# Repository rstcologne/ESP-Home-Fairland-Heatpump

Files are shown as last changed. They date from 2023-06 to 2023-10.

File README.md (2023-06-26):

# ESP-Home-Fairland-Heatpump

I'd like to share my approach to control a Fairland made heatpump directly via modbus not depending on Tuya with homeassistant. My heatpump is an IPS Pro model sold by Pool Systems which seems to be quite similar to the InverX series by Fairland directly. 

## Disclaimer

Everything I describe here is at quality level "works for me". Follow these instructions at your own risk. You need to open your heatpump and connect cables to the mains powered main crontrol board. It might void your warranty and you will get close to mains powered components including some large capacitors. Don't follow allong if you are not sure what you are doing. 

## Preparing the ESP Home board
### Components used:
- ESP Baord. Most will work
- MAX485 module, preferably one with automatic flow control
- Buck converter if the 12V from the heatpump control board will be used to power the ESP
- JST-XH 4 pin connector to attach everything to the control board
- other connectors (optional) to alow for easier disassembly

### Wiring
- 12V+ from control board to + on the buck converter input side
- Ground from control board to - on the buck converter input side
- out + from buck converter to 5V or VIN of the ESP board
- out - from buck converter to GND on the ESP board
- RX on ESP to RXD on max485 board
- TX on ESP to TXD on max485 board
- 3,3v on ESP to VCC on max485  board
- G on ESP to GND on max485 board
- A on max485 board to A on control board
- B on max485 board to B on control board

If you use a variable voltage buck converter, make sure to set it properly to deliver 5v from 12v input before connecting it to the ESP. Otherwise you might fry the board. 

In case you are using a max485 board without automatic flow control, one additional pin needs to be connected to the two center pins on the max board. This needs to be configured in esphome as well. 

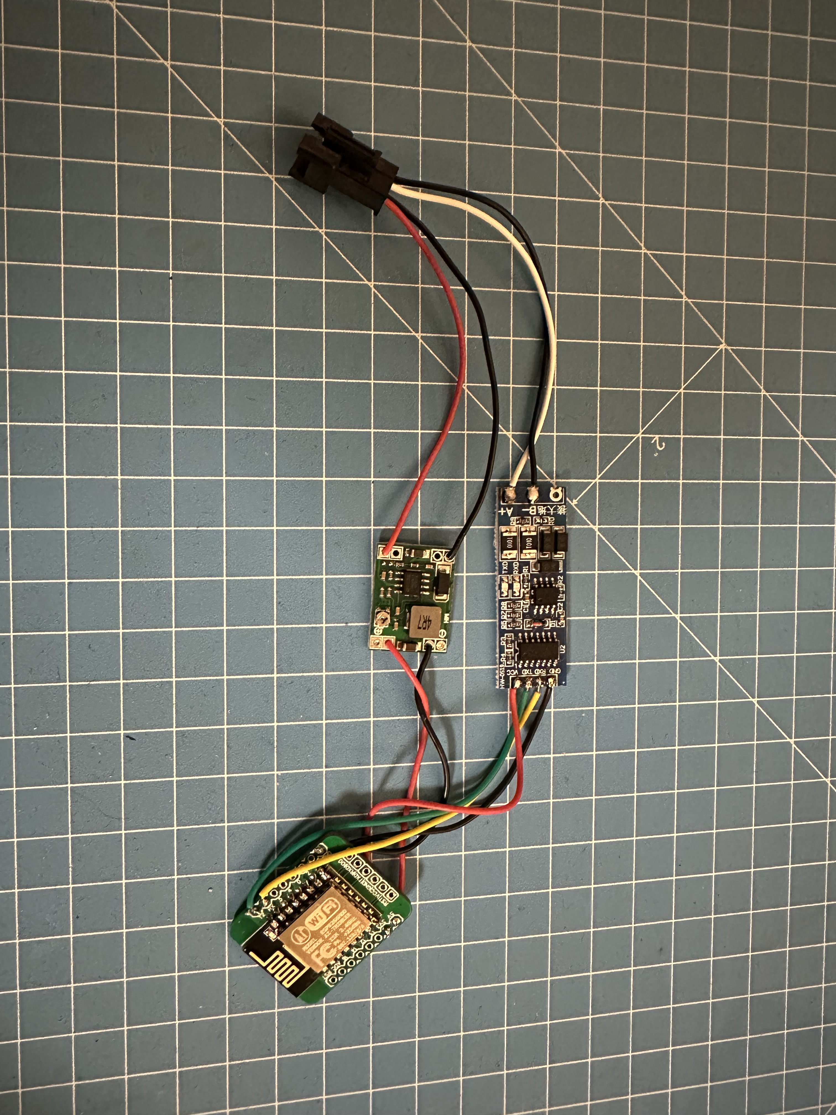
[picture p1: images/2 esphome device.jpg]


## ESP-Home
1. Create a new ESPHome device in homeassistant
2. Copy the esphome config snippet below the header. I left the captive_portal directive in the snippet for reference. Make sure it's only there once.
3. Flash the board

## Connecting to heatpump
Connect everything to the header in the center of the image marked B A G +12V. The existing cable channels are quite handy to feed the cable out at the back of the unit. I have included a very simple (temporary) housing for the electronics which I clip on to one of the 50mm water pipes. 

### How to open the heatpump (for my unit)
- Open the side panel providing access to the power connection terminal with two screws at the bottom
- two additional screws free the panel above which houses the control unit. remove this panel and disconnect the control unit
- Remove the two screws holding the top plate. There's an additional screw at the back to remove. After that, the top can be lifted.
- There's a large padded box in the center of the unit. Open it and inside you'll find the control board

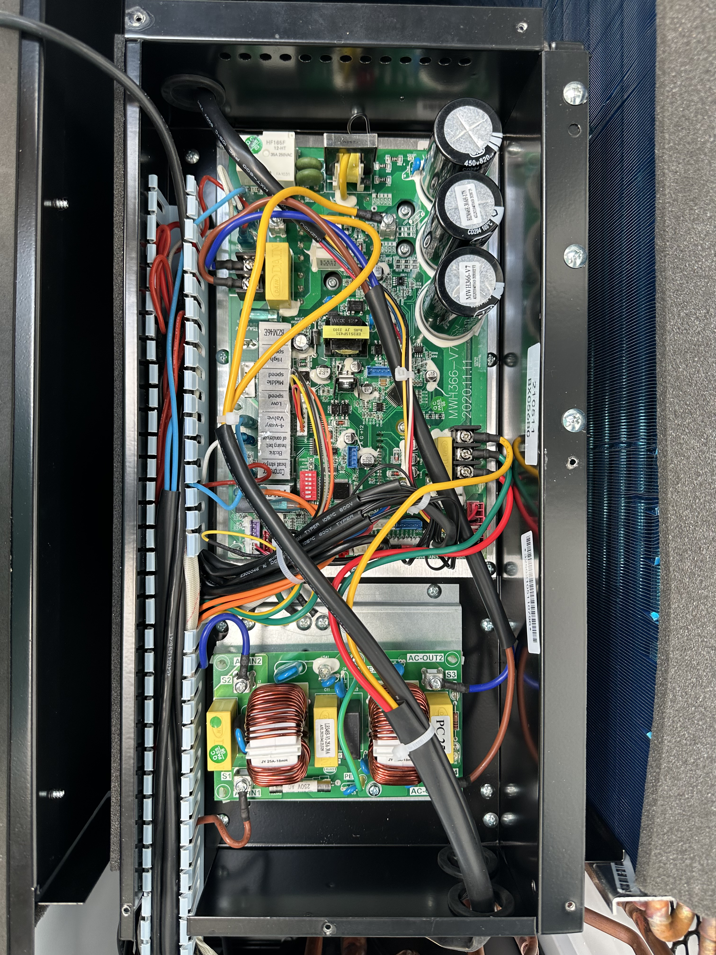
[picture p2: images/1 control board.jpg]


## Dashboard
I have added a code snippet you can incorporate in your dashboard. 
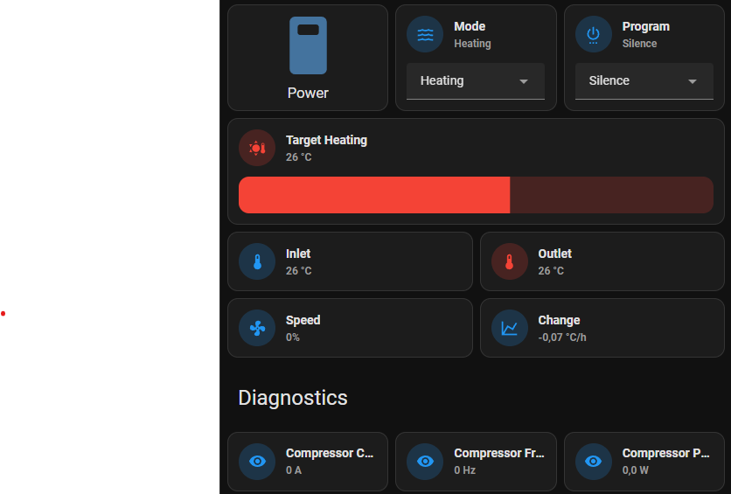
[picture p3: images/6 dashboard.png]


### Known issues
- The modbus configuration still throws a few warnings related to duplicate entries. It seems to work well despite these warnings though.
- The selected heating/cooling mode (slient, normal, ...) is not remembered properly. The heatpumpt often switches to silent when it's powered on even though normal was selected before.
- The case is to be considered rather preliminary. I just wanted something to get it to work.

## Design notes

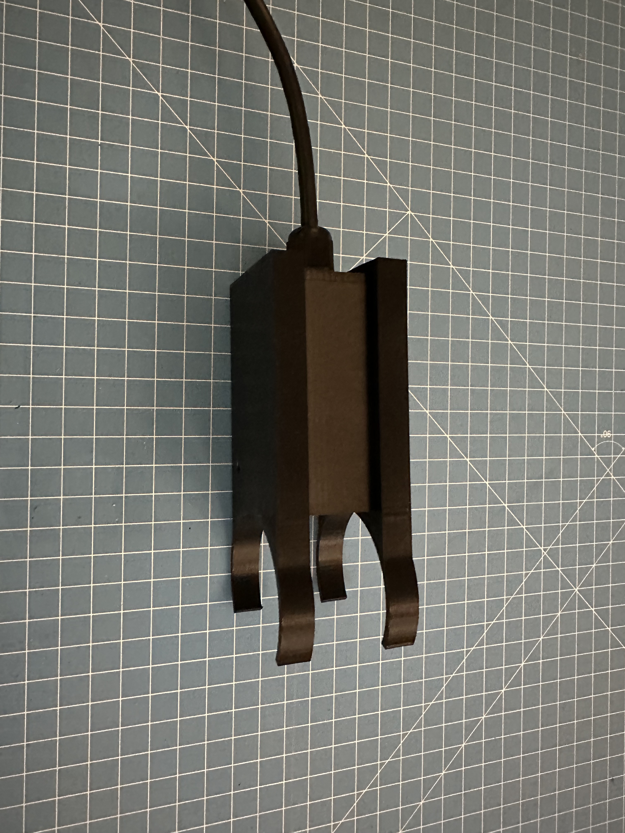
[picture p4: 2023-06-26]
images/4 case 2.jpg

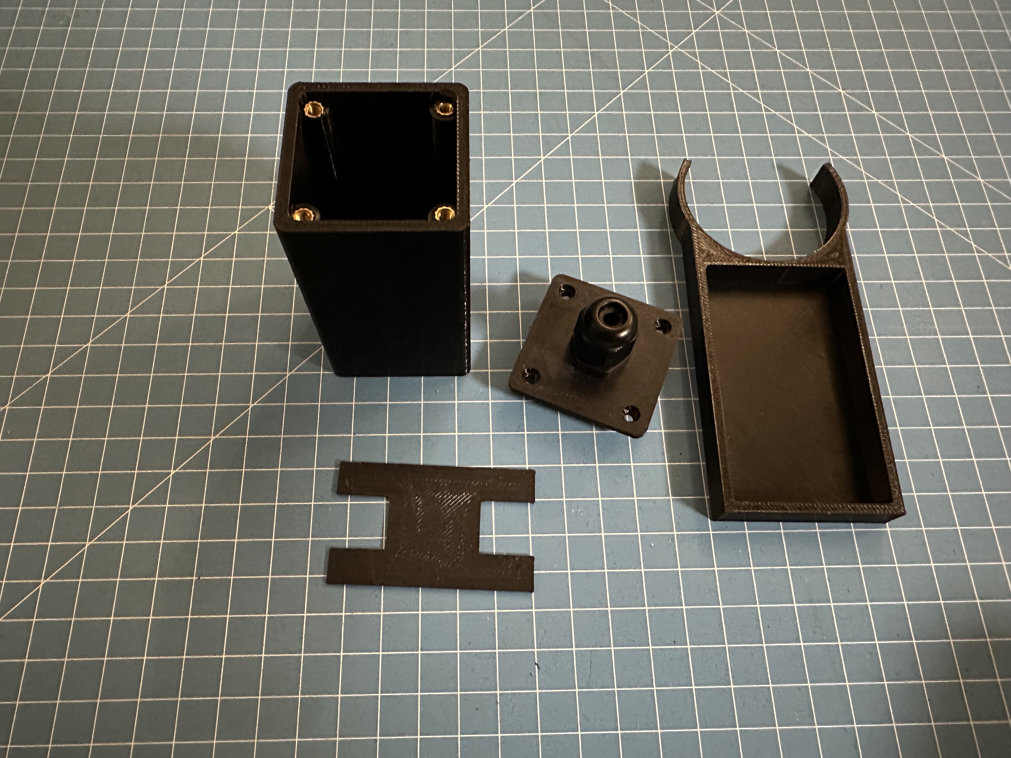
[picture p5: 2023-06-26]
images/3 case 1.jpg

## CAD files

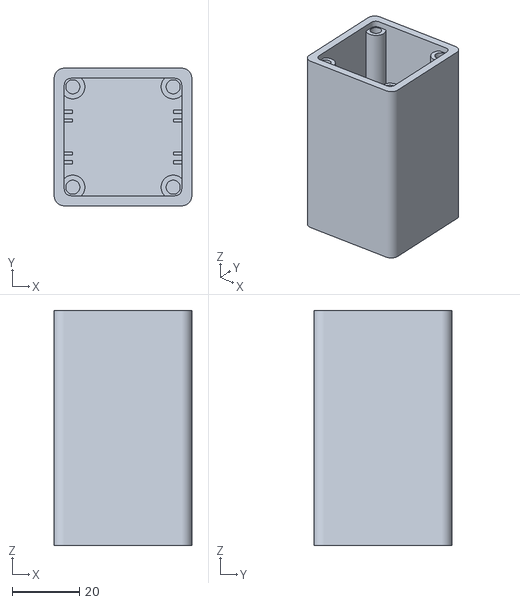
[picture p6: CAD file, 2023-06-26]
case/PoolPump_Electronics-Case.stl
41.0 x 41.0 x 70.0

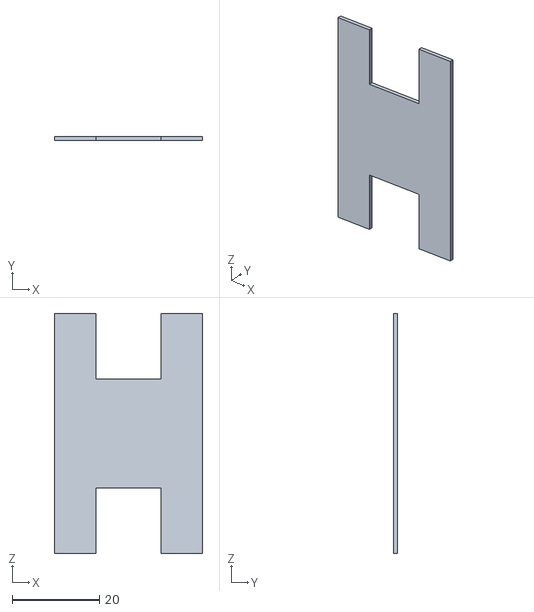
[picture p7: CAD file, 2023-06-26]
case/PoolPump_Electronics-Divider.stl
34.0 x 1.00 x 55.0

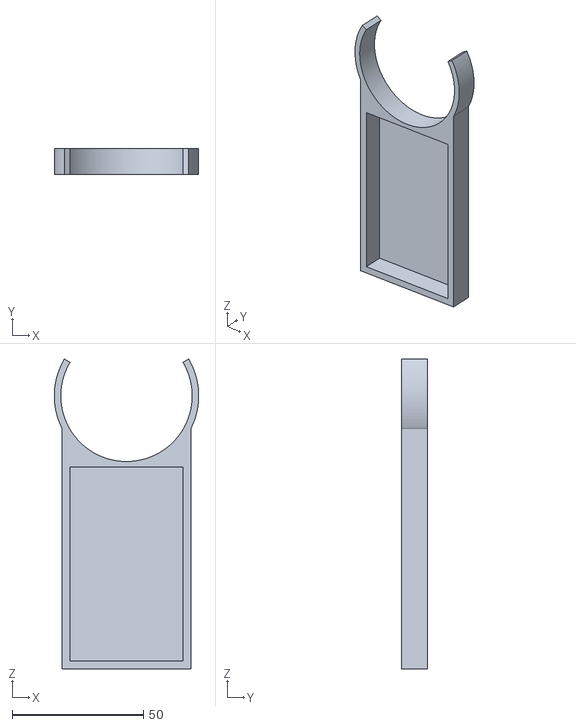
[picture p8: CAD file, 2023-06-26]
case/PoolPump_Electronics-Mount.stl
55.0 x 10.0 x 118.0

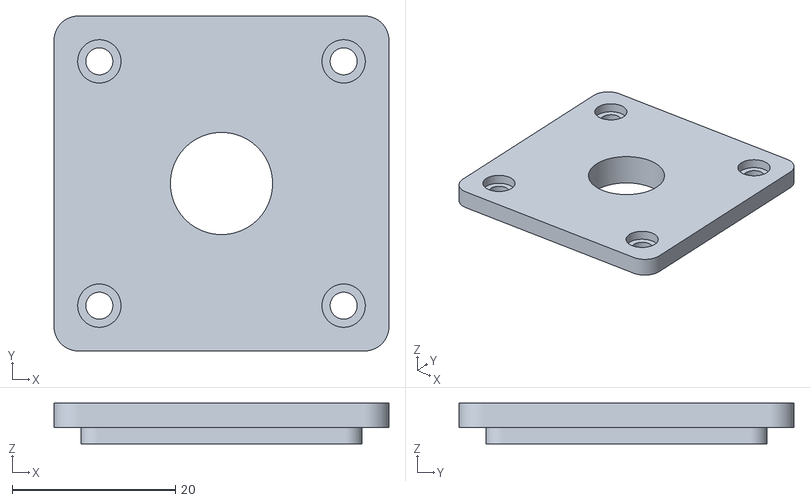
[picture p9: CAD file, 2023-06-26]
case/PoolPump_Electronics-Lid.stl
41.0 x 41.0 x 5.00

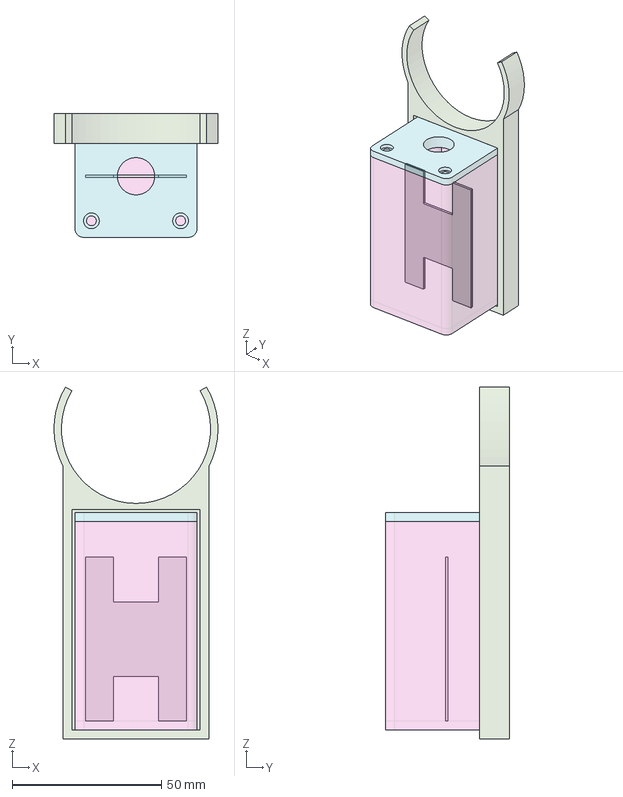
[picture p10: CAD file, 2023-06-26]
case/PoolPump_Electronics.FCStd
55.0 x 41.5 x 118.0 mm
Case
Lid
Mount
Divider

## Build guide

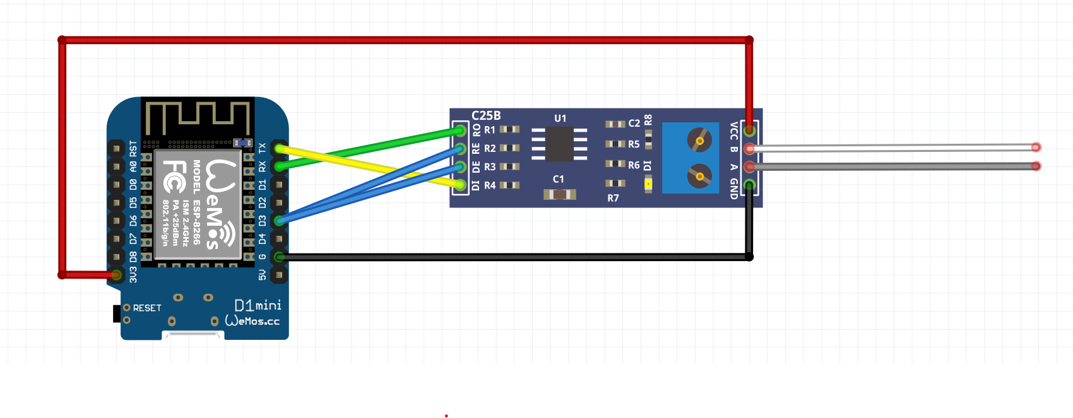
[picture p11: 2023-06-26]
images/5 wiring.png

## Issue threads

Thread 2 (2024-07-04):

Compatibility with other Tuya comatible Heatpumps

chrisguen, 2024-07-04:
Hello, has anyone tested if this project works with other wifi/tuya enabled heatpumps like [this](https://www.poolmegastore.de/poolheizung/waermepumpen/full-inverter-waermepumpen/evolution-proline/full-inverter-waermepumpe-evolution-proline-7.html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) one?

raspitoaster, 2024-07-09:
Hi, I am testing with a "Evolution Baseline" - but without success yet.
There are two RS485 sockets on the  circuit board. The #1 is empty, the #2 has the front panel (display/buttons) and WiFi connected.
Using the YAML here on a NodeMCUv2 (ESP8266/4M) connected to a RS485-2-TTL converter results in many "Duplicate modbus command found" warnings and (only) silly sensor readings.
I tested the setup (NodeMCU/ESPHome/RS485-2-TTL converter) connected to a second RS485-2-TTL converter and a RASPI with pyModSlave simulating a modbus device. This works perfectly, but there are many posts around that claim ESP8266 with software serial will not work at all and ESP32 with hardware serial must be used.

raspitoaster, 2024-07-10:
Update: just tried with an ESP32 and hardware serial ... same result.

poorredneck, 2025-07-23:
Works great on my Raypak (Rheem) Crosswinds 65i.
Board is similar but not the same, same blue JST "BAG +12" connector.

poorredneck, 2025-07-23:
@raspitoaster were you asking OP or me? Mine is no different than the original from rstcologne, all the registers lined up. I dont have a way of checking the error codes, but the E3 for no water flow does work correctly, as well as all the temperatures and set point/mode adjustments. The Raypak does not have a "Turbo" mode. I also didn't know mine had "Super Silent" that option was not available in the app or on the LCD interface but does work via the ModBus commands.

Incase you were asking me and not OP, here is my config.

```
esphome:
  name: poolheater
  friendly_name: Pool Heater

esp8266:
  board: d1_mini

wifi:
  ssid: "Repeater"
  password: !secret wifi_pw
  ap:
    ssid: "PoolHeater Fallback AP"
    password: "fallback123"

logger:
  level: DEBUG

api:
  encryption:
    key: !secret encrypt1

ota:
  - platform: esphome

####
## Create a new ESP-Home Device and paste the snippet below into the newly created config.
## make sure, captive portal is only in the file once (if you want to keep it in the first place)
####

uart:
  id: mod_bus
  rx_pin: D2
  tx_pin: D1
  baud_rate: 9600

modbus:
#  flow_control_pin: GPIO4
  id: modbus1

modbus_controller:
  - id: fairland
    ## the Modbus device addr
    address: 0x0001
    modbus_id: modbus1
    update_interval: 10s

###################################################
# Elements with Modbus Operation read 01 / write 05
# coil
###################################################
# 0	Power
# 1	compulsory defrosting
# 2～47	reserve
###################################################

switch:
  - platform: modbus_controller
    modbus_controller_id: fairland
    name: "PWP Power Switch"
    id: pwp_power_switch
    register_type: coil
    address: 0x0
    # unit_of_measurement: "State"

###################################################
# Elements with Modbus Operation read 03 / write 06
# holding
###################################################
# address content	Range	Unit	Step length	Defaut	Illustration
# 0	mode selectioin 1	0～2				0：Auto，1：Heating，2：Cooling
# 1	mode selectioin 2	0～3		1	1	0：Normal，1：silence，2：Super silence, 3: Turbo
# 2	Temp setting under Auto mode	18~35	℃	1	25
# 3	Temp setting under heating mode
# 4	Temp setting under cooling mode	30~95	%	1	50
# 5	Running mode of water pump	0~2		1	0	"0：Continuation
# 1：Water temp control
# 2：time/water temp control
# "
# 6	Time setting of water pump (When under running mode 2)	10 ~ 120 	min	5	60
# 7	The compressor runs continuously before defrosting enters	20~90	min	1	20
# 8	Defrosting start temp	-10~10	℃	1	-1
# 9	Defrosting running time	1~12	min	1	8
# 10	Defrosting quit temp	0~30	℃	1	8
# 11	Fixed speed mode selection
# 12	reserve
# 13	reserve
# 14	Low temperature shutdown protection correction amount
# 12	reserve
# 13	reserve
# 17	Electronic expansion valve overheat level（heating）	-10~20	℃	1	3
# 18	Electronic expansion valve overheat level（cooling）	-10~20	℃	1	3
# 19	Electronic expansion valve manual/auto	0~1		1	0	0：auto，1：Manual
# 20	Electronic expansion valve openning setting（heating）	50~240		2	100
# 21	Electronic expansion valve openning setting（cooling）	50~240		2	100
# 22	The medium frequency ratio selection
# 23	reserve
# 24	reserve
# 25	Power off memory function	0~1		1	1	0: None;  1: Yes
# 26	reserve
# 27	reserve
# 28	reserve
# 29	reserve
# 30	reserve
# 31	reserve
# 32	reserve
###################################################

select:
  - platform: modbus_controller
    name: "PWP Operating Mode"
    id: pwp_operating_mode
    modbus_controller_id: fairland
    address: 0x0
    value_type: U_WORD
    optionsmap:
      "Auto": 0
      "Heating": 1
      "Cooling": 2

  - platform: modbus_controller
    name: "PWP Power Mode"
    id: pwp_power_mode
    modbus_controller_id: fairland
    address: 0x1
    value_type: U_WORD
    optionsmap:
      "Super Silence": 2
      "Silence": 1
      "Normal": 0
      "Turbo": 3

# Temperature Formula
# ((value - 96) / 2) + 18

number:
  - platform: modbus_controller
    modbus_controller_id: fairland
    name: "PWP Target Temperature Heating"
    id: pwp_target_temperature_heating
    register_type: holding
    address: 0x3
    value_type: U_WORD
    unit_of_measurement: "°F"
    min_value: 64        # 18 °C → 64.4 °F, rounded to 64
    max_value: 104     # 32 °C → 89.6 °F, rounded to 90
    step: 1              # only allow integer °F steps
    lambda: |-
      // read raw R → °F, rounded to nearest integer
      return round((x - 60) * 0.9 + 32);
    write_lambda: |-
      // take integer °F → raw R
      float raw = (x - 32) / 0.9 + 60;
      return (uint16_t)raw;

  - platform: modbus_controller
    modbus_controller_id: fairland
    name: "PWP Target Temperature Auto"
    id: pwp_target_temperature_auto
    register_type: holding
    address: 0x2
    value_type: U_WORD
    unit_of_measurement: "°F"
    min_value: 54        # 18 °C → 64.4 °F → 64 °F
    max_value: 104        # 32 °C → 89.6 °F → 90 °F
    step: 1
    lambda: |-
      // raw R → °F: round((R–60)/2×1.8 + 32)
      return round((x - 60) * 0.9 + 32);
    write_lambda: |-
      // °F → raw R: (F–32)/0.9 + 60
      float raw = (x - 32) / 0.9 + 60;
      return (uint16_t)raw;

  - platform: modbus_controller
    modbus_controller_id: fairland
    name: "PWP Target Temperature Cooling"
    id: pwp_target_temperature_cooling
    register_type: holding
    address: 0x4
    value_type: U_WORD
    unit_of_measurement: "°F"
    min_value: 54        # 18 °C → 64.4 °F → 64 °F
    max_value: 86        # 32 °C → 89.6 °F → 90 °F
    step: 1
    lambda: |-
      // raw R → °F: round((R–60)/2×1.8 + 32)
      return round((x - 60) * 0.9 + 32);
    write_lambda: |-
      // °F → raw R: (F–32)/0.9 + 60
      float raw = (x - 32) / 0.9 + 60;
      return (uint16_t)raw;

###################################################
# Elements with Modbus Operation read 04 / write NA
# read
###################################################
# 0	Percentage of speed
# 1	Target frequency of compressor
# 2	Voltage of PFC
# 3	Inlet water temp
# 4	Outlet water temp
# 5	Ambient air temp
# 6	Dircharge temp
# 7	Outer coil pipe temp
# 8	Suction temp
# 9	Inner coil pipe tem
# 10	Running frequency of compressor
# 11	Current of compressor
# 12	Cooling plate temp
# 13	Electronic expansion valve opening
# 14	DC fan speed
# 15	Lower limit of setting temp of auto mode
# 16	Upper limit of setting temp of auto mode
# 17	Lower limit of setting temp of heating mode
# 18	Upper limit of setting temp of heating mode
# 19	Lower limit of setting temp of cooling mode
# 20	Upper limit of setting temp of cooling mode
# 21	Motherboard version code1					ASCII code
# 22	Motherboard version code2					ASCII code
# 23	Motherboard version code3					ASCII code
# 24	Motherboard version code4					ASCII code
# 25	Motherboard version code5					ASCII code
# 26	Model code1					ASCII code
# 27	Model code2 ('C'is heating and cooling version，‘H’is heating version)					ASCII code
# 28	Model code3					ASCII code
# 29	Model code4					ASCII code
# 30	Voltage of power supply		V	1
# 31	The remaining time of Compressor shutdown protection 		S	1
# 32	reserve
###################################################

sensor:

  - platform: modbus_controller
    modbus_controller_id: fairland
    name: "PWP Speed Percentage"
    id: pwp_speed_percentage
    register_type: read
    address: 0x0
    value_type: U_WORD
    unit_of_measurement: "%"

  - platform: modbus_controller
    modbus_controller_id: fairland
    name: “Voltage of PFC”
    id: voltage_of_pfc
    register_type: read
    address: 0x2
    value_type: U_WORD
    unit_of_measurement: "V"

  - platform: modbus_controller
    modbus_controller_id: fairland
    name: "PWP Inlet Water Temperature"
    id: pwp_inlet_water_temperature
    register_type: read
    address: 0x3
    value_type: U_WORD
    unit_of_measurement: "°F"
    filters:
      - offset: -60      # (raw – 60)
      - multiply: 0.9    # × 0.9 → (raw–60)/2×1.8
      - offset: 32       # + 32 to finish °C→°F

  - platform: modbus_controller
    modbus_controller_id: fairland
    name: "PWP Outlet Water Temperature"
    id: pwp_outlet_water_temperature
    register_type: read
    address: 0x4
    value_type: U_WORD
    unit_of_measurement: "°F"
    filters:
      - offset: -60
      - multiply: 0.9
      - offset: 32

  - platform: modbus_controller
    modbus_controller_id: fairland
    name: "PWP Compressor Current"
    id: pwp_compressor_current
    register_type: read
    address: 11
    value_type: U_WORD
    unit_of_measurement: "A"
    filters:
      - multiply: 0.1

  - platform: modbus_controller
    modbus_controller_id: fairland
    name: "PWP Compressor Running Frequency"
    id: pwp_compressor_running_frequency
    register_type: read
    address: 10
    value_type: U_WORD
    unit_of_measurement: "Hz"

  # Thanks to oseldusan1 in homeassistant community for the fix to
  # use PFC Voltage for power consumption calculation.
  - platform: template
    name: "PWP Compressor Power"
    id: pwp_compressor_power
    unit_of_measurement: "W"
    lambda: |-
      if (id(pwp_compressor_current).state) {
      return id(pwp_compressor_current).state * id(voltage_of_pfc).state;
      } else {
      return 0.0;
      }
    update_interval: 1s

###################################################
# Elements with Modbus Operation read 02 / write NA
# discrete_input
###################################################
# 0	Switch on/off
# 1	Defrosting
# 2	Temperature adjustment
# 3	Silence
# 4	Anti-freeze
# 5	Cooling mode selection
# 6	Remote controll
# 7	Water flow swtich
# 8	High pressure swtich
# 9	Low pressure swtich
# 10	Compressor
# 11	Outdorr fan motor
# 12	4-Way valve
# 13	Bypass valve
# 14	reserve
# 15	Heating element in the basis
# 16	reserve
# 17	Circulation pump
# 17～47	reserve
# 48	E0
# 49	E1
# 50	E2
# 51	E3
# 52	E4
# 53	E5
# 54	E6
# 55	E7
# 56	E8
# 57	E9
# 58	EA
# 59	EB
# 60	EC
# 61	ED
# 62	EE
# 63	EF
# 64	P0
# 65	P1
# 66	P2
# 67	P3
# 68	P4
# 69	P5
# 70	P6
# 71	P7
# 72	P8
# 73	P9
# 74	PA
# 75	PB
# 76	PC
# 77	PD
# 78	PE
# 79	PF
# 80	F0
# 81	F1
# 82	F2
# 83	F3
# 84	F4
# 85	F5
# 86	F6
# 87	F7
# 88	F8
# 89	F9
# 90	FA
# 91	FB
# 92	FC
# 93	FD
# 94	FE
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
raspitoaster, 2025-07-24:
> were you asking OP or me? Mine is no different than the original from rstcologne, all the registers lined up

I was asking you because this issue here discusses the heat pumps branded as "Evolution".
Thanks for you config - but this is for "standard" Fairlands and will not work with the "Evolution" ones.

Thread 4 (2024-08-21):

counterintuitive formula for temperature conversion

kriede, 2024-08-21:
You are using a counterintuitive formular:

`degree = ((response.registers[0] - 96) / 2) + 18`

what can be rewritten as

`degree = -30 + response.registers[0] / 2`

or

`degree = (response.registers[0] -60) / 2`

Maybe not a big deal but clarifies what is really happening here: possible values...
- start at -30°C
- go up in steps of 0.5°C
- go up to 97.5°C (using 7-bits)

what fits all use-cases af such a heat pump.

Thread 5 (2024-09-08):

Has anyone tested this project with this board LilyGo Tcan485 Esp32 RS485

niklas-a, 2024-09-08:
Hi! I am interested in this project and am planning to give it a go.

Has anyone tested it with this board? It seems to both support modbus, ESP32 and 5-12V in.
https://www.tindie.com/products/lilygo/lilygo-ttgo-t-can485-esp32-can-rs-485/

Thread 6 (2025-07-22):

Readings in *F?

poorredneck, 2025-07-22:
I should report this works great on the Raypak Crosswinds 65000 BTU inverter heater as well. Board is very similar but different. Same RA485 blue JST connector.

I wish I understood how the temp reporting works. Without having to create duplicate template sensors how can I have all temps report and editable set temp in Fahrenheit?

THANK YOU for this, love all the extra data and no more stupid Tuya!!!

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

Closed 2025-07-23.

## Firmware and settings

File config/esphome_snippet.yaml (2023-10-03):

####
## Create a new ESP-Home Device and paste the snippet below into the newly created config. 
## make sure, captive portal is only in the file once (if you want to keep it in the first place)
####



captive_portal:

web_server:
  port: 80


uart:
  id: mod_bus
  rx_pin: RX
  tx_pin: TX
  baud_rate: 9600
  
modbus:
#  flow_control_pin: GPIO4
  id: modbus1

modbus_controller:
  - id: fairland
    ## the Modbus device addr
    address: 0x0001
    modbus_id: modbus1
    update_interval: 2s

###################################################
# Elements with Modbus Operation read 01 / write 05
# coil
###################################################
# 0	Power
# 1	compulsory defrosting
# 2～47	reserve
###################################################

switch:
  - platform: modbus_controller
    modbus_controller_id: fairland
    name: "PWP Power Switch"
    id: pwp_power_switch
    register_type: coil
    address: 0x0
    # unit_of_measurement: "State"



###################################################
# Elements with Modbus Operation read 03 / write 06
# holding
###################################################
# address content	Range	Unit	Step length	Defaut	Illustration
# 0	mode selectioin 1	0～2				0：Auto，1：Heating，2：Cooling
# 1	mode selectioin 2	0～3		1	1	0：Normal，1：silence，2：Super silence, 3: Turbo
# 2	Temp setting under Auto mode	18~35	℃	1	25	
# 3	Temp setting under heating mode					
# 4	Temp setting under cooling mode	30~95	%	1	50	
# 5	Running mode of water pump	0~2		1	0	"0：Continuation 
# 1：Water temp control
# 2：time/water temp control
# "
# 6	Time setting of water pump (When under running mode 2)	10 ~ 120 	min	5	60	
# 7	The compressor runs continuously before defrosting enters	20~90	min	1	20	
# 8	Defrosting start temp	-10~10	℃	1	-1	
# 9	Defrosting running time	1~12	min	1	8	
# 10	Defrosting quit temp	0~30	℃	1	8	
# 11	Fixed speed mode selection					
# 12	reserve					
# 13	reserve					
# 14	Low temperature shutdown protection correction amount					
# 12	reserve					
# 13	reserve					
# 17	Electronic expansion valve overheat level（heating）	-10~20	℃	1	3	
# 18	Electronic expansion valve overheat level（cooling）	-10~20	℃	1	3	
# 19	Electronic expansion valve manual/auto	0~1		1	0	0：auto，1：Manual
# 20	Electronic expansion valve openning setting（heating）	50~240		2	100	
# 21	Electronic expansion valve openning setting（cooling）	50~240		2	100	
# 22	The medium frequency ratio selection					
# 23	reserve					
# 24	reserve					
# 25	Power off memory function	0~1		1	1	0: None;  1: Yes  
# 26	reserve					
# 27	reserve					
# 28	reserve					
# 29	reserve					
# 30	reserve					
# 31	reserve					
# 32	reserve					
###################################################

select:
  - platform: modbus_controller
    name: "PWP Operating Mode"
    id: pwp_operating_mode
    modbus_controller_id: fairland
    address: 0x0
    value_type: U_WORD
    optionsmap: 
      "Auto": 0
      "Heating": 1
      "Cooling": 2
    
  - platform: modbus_controller
    name: "PWP Power Mode"
    id: pwp_power_mode
    modbus_controller_id: fairland
    address: 0x1
    value_type: U_WORD
    optionsmap: 
      "Super Silence": 2
      "Silence": 1
      "Normal": 0
      "Turbo": 3

# Temperature Formula
# ((value - 96) / 2) + 18

number:
  - platform: modbus_controller
    modbus_controller_id: fairland
    name: "PWP Target Temperature Heating"
    id: pwp_target_temperature_heating
    address: 0x3
    value_type: U_WORD
    unit_of_measurement: "°C"
    min_value: 18
    max_value: 32
    lambda: "return (x-96) / 2 + 18;"
    write_lambda: |- 
      ESP_LOGD("main", "Modbus Number incoming value = %f", x);
      return ((x-18) * 2 + 96) * 1.0;

  - platform: modbus_controller
    modbus_controller_id: fairland
    name: "PWP Target Temperature Auto"
    id: pwp_target_temperature_auto
    register_type: holding
    address: 0x2
    value_type: U_WORD
    unit_of_measurement: "°C"
    min_value: 18
    max_value: 32
    lambda: "return (x-96) / 2 + 18;"
    write_lambda: |- 
      ESP_LOGD("main", "Modbus Number incoming value = %f", x);
      return ((x-18) * 2 + 96) * 1.0;

  - platform: modbus_controller
    modbus_controller_id: fairland
    name: "PWP Target Temperature Cooling"
    id: pwp_target_temperature_cooling
    register_type: holding
    address: 0x4
    value_type: U_WORD
    unit_of_measurement: "°C"
    min_value: 18
    max_value: 32
    lambda: "return (x-96) / 2 + 18;"
    write_lambda: |- 
      ESP_LOGD("main", "Modbus Number incoming value = %f", x);
      return ((x-18) * 2 + 96) * 1.0;
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

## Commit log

2023-06-26 initial
    initial
    [PoolPump_Electronics-Case.stl, PoolPump_Electronics-Divider.stl, PoolPump_Electronics-Lid.stl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]
2023-10-03 Use PFC Power for compressor power consumption
2023-10-03 add pfc fix attribution
    [esphome_snippet.yaml]
